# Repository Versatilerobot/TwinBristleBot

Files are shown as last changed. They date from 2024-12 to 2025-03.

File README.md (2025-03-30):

# TwinBristleBot
Vibration-driven locomotion robot <br />
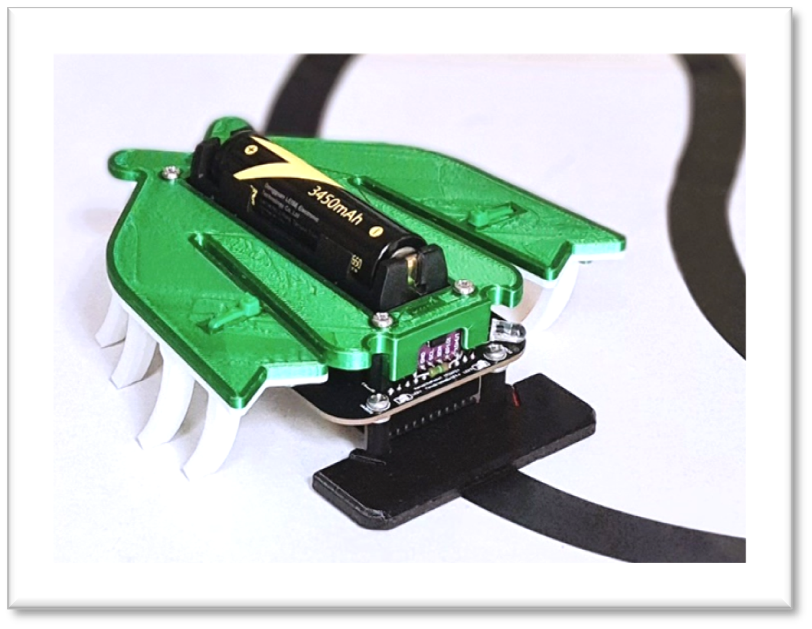
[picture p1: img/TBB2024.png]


# Présentation
La TBB#3 est la troisiéme génération d'un robot propulsé et dirigé par vibrations. Dans ce dossier vous trouverez toutes les informations pour le construire et le programmer en mode suiveur de ligne, mais on peut aussi le téléopérer par Bluetooth. 

Vous trouverez une vidéo de démonstration au lien suivant :
https://youtu.be/ebChETA49Jo

# Historique
Le premier modèle de 2010 avait été conçu à l’aide d’une brosse à balais et un Arduino UNO. Il a fait l’objet d’un tutorial d’assemblage dans la revue Française Planète Robots N°11 à 13. Avec son aspect « SteamPunk » elle a parcouru de longues distances sur les salons.

La deuxième génération de 2016 avait pour objectif d’en faire un kit éducatif pour l’association Française de robotique Caliban https://www.facebook.com/AssoCaliban et pouvait être commandée en Bluetooth par un smartphone. Plus légère et plus rapide elle utilisait des filaments de coupe bordure pour se propulser. Mais son assemblage était assez laborieux et il y avait besoin de plusieurs grosses batteries.
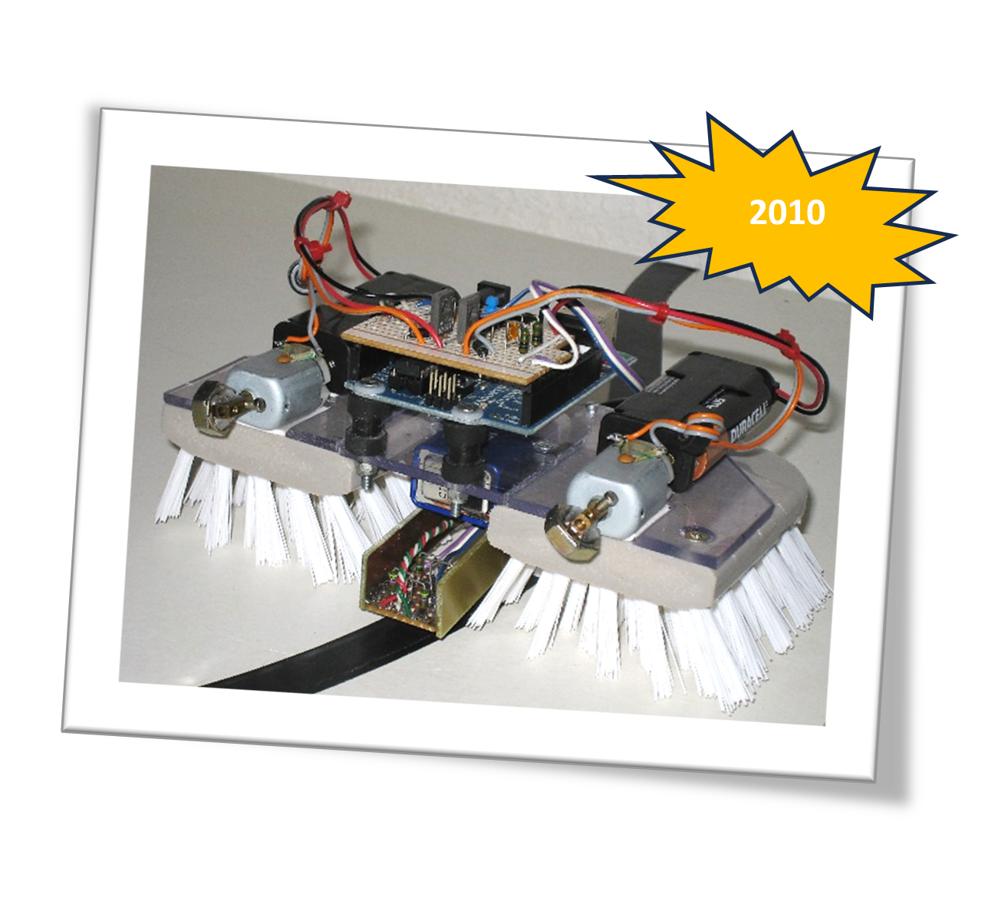
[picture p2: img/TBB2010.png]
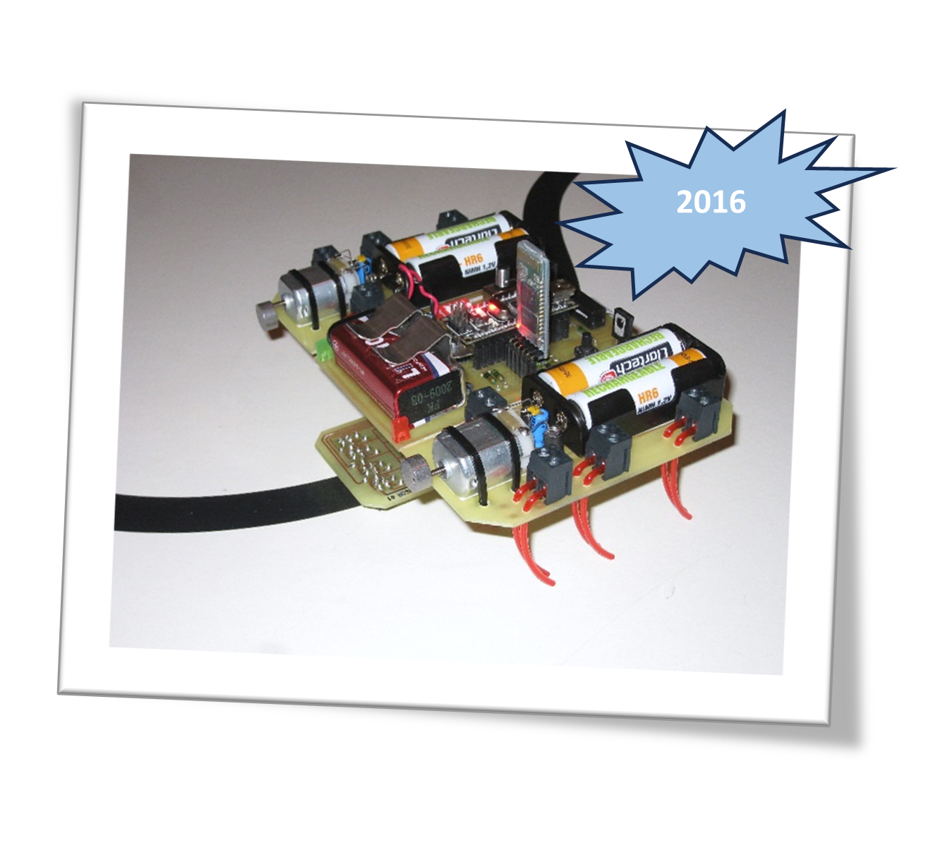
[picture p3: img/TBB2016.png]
 
<br /> Vous retrouverez quelques démos de ces précédentes versions aux lien suivants :<br />
Twin BristleBot 2010 : https://youtu.be/IOm3nyDv1LA?si=ABxqIedQcTU6AHdo <br />
Twin BristleBot 2016: https://youtu.be/aQ-3ZJKfJKs?si=AR1gLndqPDY5ka6K

# Nouvelle version TBB#3
La version de 2024 est conçue en impression 3D PLA pour le corps et en TPU pour les pattes. 
<br /> Tous les plans STL sont fournis.

Le robot est en plus équipé d’un module de télémétrie IR qui utilise la technologie Time Of Flight afin de détecter les obstacles devant lui tel qu'un autre robot ou une barriére. Les vibrations sont générées par deux micro-moteurs à masselottes M20 placés à droite et gauche sous le corps, ce qui permet de diriger le robot. Il a aussi en option la capacité d'émettre et recevoir un code d’indentification IR dont la portée est ajustable électroniquement pour s'identifier et faire évoluer plusieurs robots sur une piste avec croisements. Son module de commande utilise un objet IoT open-source T-Energy équipé d’un ESP32 WROVER-B 240MHZ et qui est alimenté par une batterie 3.7V Li-ion 18650. Le module comporte un connecteur micro USB pour la recharge et la programmation, ainsi qu’un interrupteur d’alimentation.

Pour faire le lien entre le module de commande et les autres composants tel que les moteurs et capteurs j’ai dessiné un PCB double face que j’ai fait réaliser en ligne par JLCPCB https://jlcpcb.com/, mais vous pouvez utiliser tout autre fournisseur.

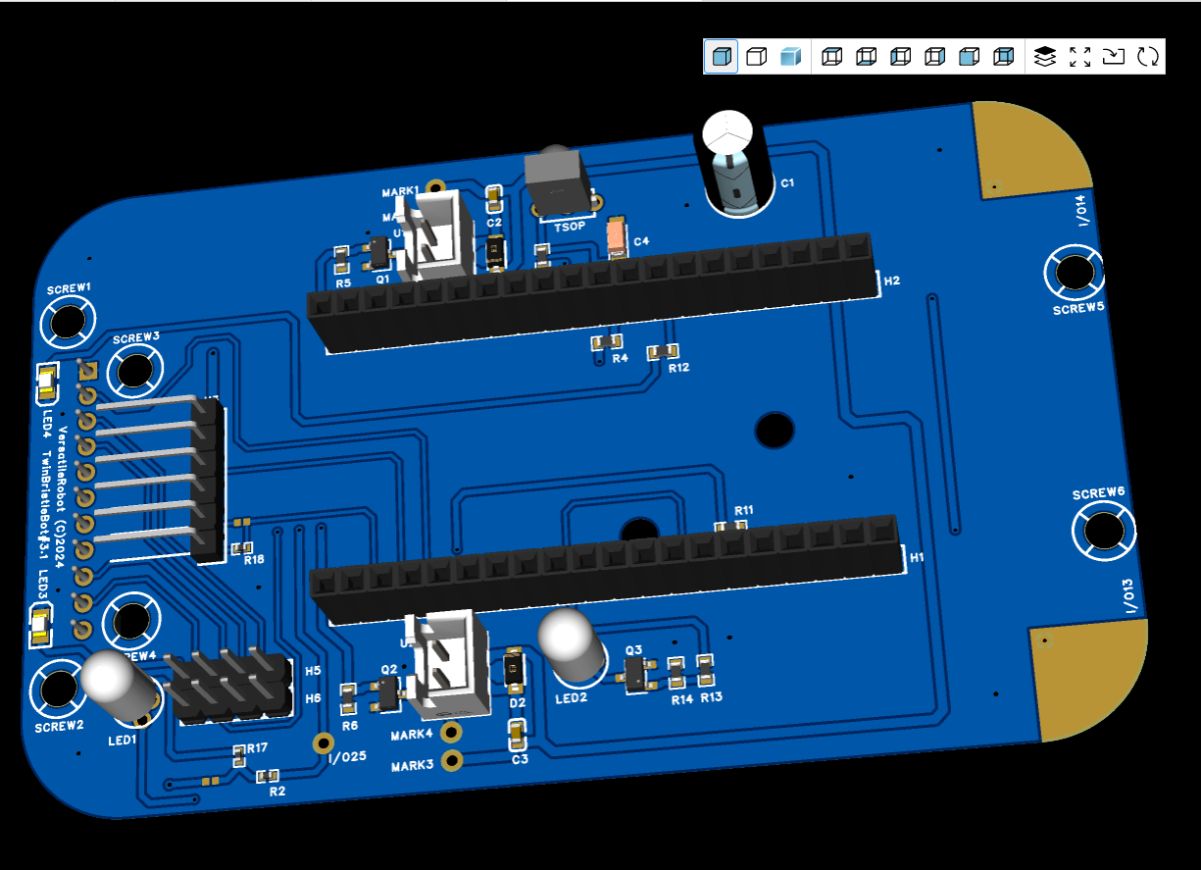
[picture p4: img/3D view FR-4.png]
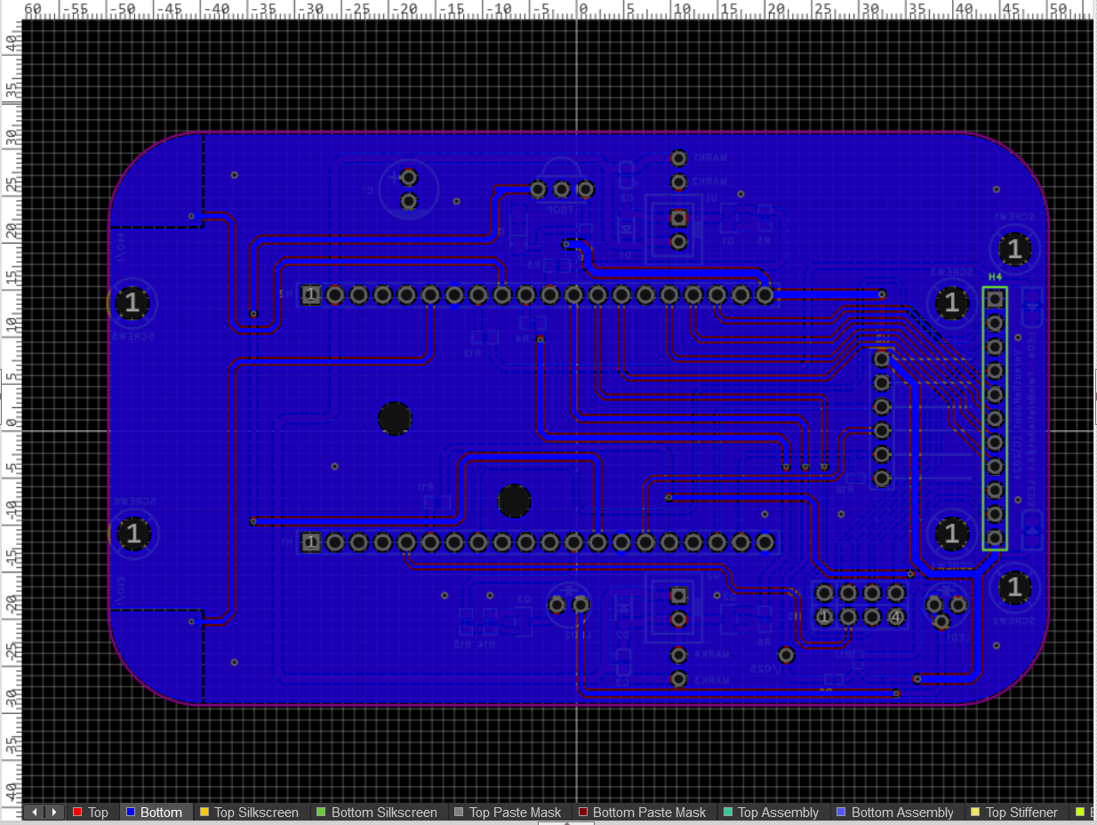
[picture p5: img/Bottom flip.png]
 

Le schéma électronique, ainsi que le fichier Gerber, la BOM de composants et le fichier de placement des composants sont fournis. Pour ma part j’ai opté pour faire assembler les composants de surface SMD (Surface Mount Device), ce qui facilite l’assemblage car il reste à souder soi-même que les composants traditionnels traversants tels que les connecteurs… L’ensemble peut donc être approvisionné en ligne.

Le dossier comprend un manuel d’instructions pour l’assemblage et le démarrage, ainsi qu’un exemple de programme pour suivre une ligne et détecter des obstacles. ( ! ce programme est compatible avec le module complémentaire Expressif version 2.0.17). 
<br /> J'espère que vous apprécierez construire ce robot et si c’est le cas n’hésitez pas à mettre une étoile sur le GitHub, ça fait toujours plaisir.

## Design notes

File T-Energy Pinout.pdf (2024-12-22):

Récapitulatif des I/O possibles pour les pins de l’ESP32 (https://www.upesy.fr/blogs/tutorials/esp32-pinout-reference-gpio-pins-ultimate-guide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)
PIN | TTB#3 | Input | Output | Pullup/Pulldown/Touch pin | Commentaires

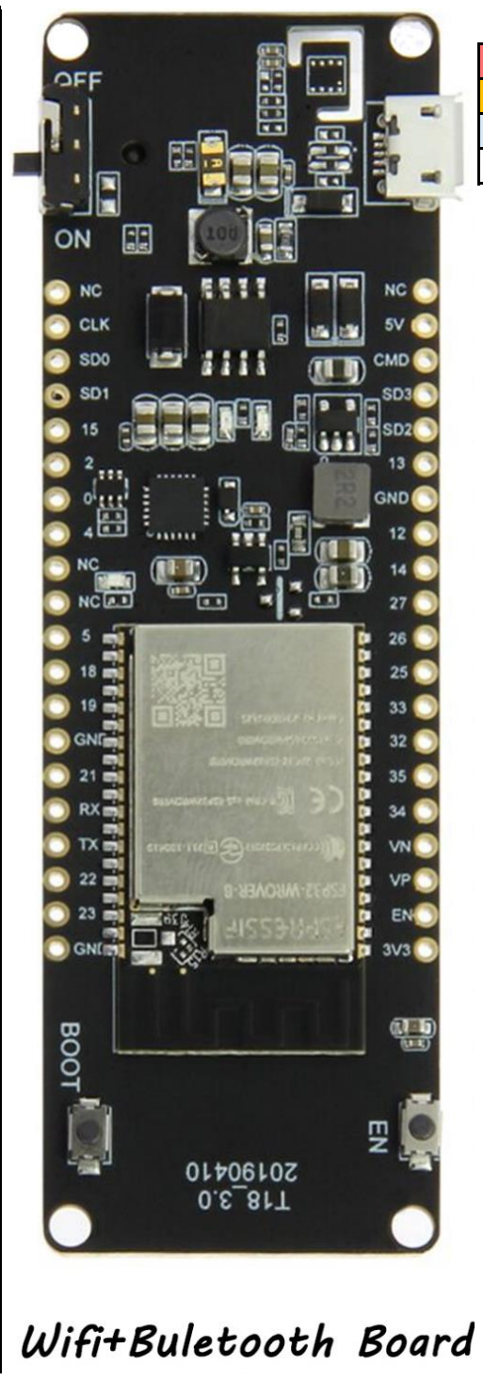
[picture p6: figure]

NC | Recommandé de ne pas utiliser
CLK | NON | NON | Connecté à la flash interne | Peut être utilisé, mais avec certaines précautions
SD0 | NON | NON | Connecté à la flash interne | Fonctionalités réduites
SD1 | NON | NON | Connecté à la flash interne | RAS
15 | Out2 line | OUI | OUI | Pullup interne / TOUCH3 | ADC2_CH3. Startup log si à 3.3V
2 | Red LED | OUI | OUI | Pulldown interne / TOUCH2 | ADC2_CH2. Doit être à 0V pendant le FLASH
0 | Bouton BOOT | OUI | OUI | Pullup interne / TOUCH1 | ADC2_CH1. Doit être à 0V pendant le FLASH
4 | IR line | OUI | OUI | TOUCH0 | ADC2_CH0
NC
NC
5 | Blue Int LED | OUI | OUI
18 | LEDs IR cde | OUI | OUI
19 | Recep IR D | OUI | OUI
GND | GND
21 | I2c ToF | OUI | OUI | | I2C - SDA
RX0 | | OUI | NON | | Communication UART avec le PC
TX0 | | NON | OUI | | Communication UART avec le PC
22 | I2c ToF | OUI | OUI | | I2C - SCL
23 | Enable ToF | OUI | OUI
GND | GND
3.3V | 3.3V
EN | Bouton EN | NON | NON | | Relié au bouton EN (ESP32 Reset)
VP (36) | Out3 line | OUI | NON | Pas de pullup/pulldown interne | ADC1_CH0 à n'utiliser qu'en entrée
VN (39) | Out4 line | OUI | NON | Pas de pullup/pulldown interne | ADC1_CH3 à n'utiliser qu'en entrée
34 | Out5 line | OUI | NON | Pas de pullup/pulldown interne | ADC1_CH6 à n'utiliser qu'en entrée
35 | Bat Voltage | OUI | NON | Pas de pullup/pulldown interne | ADC1_CH7 à n'utiliser qu'en entrée
32 | Out6 line | OUI | OUI | TOUCH9 | ADC1_CH4
33 | Out7 line | OUI | OUI | TOUCH8 | ADC1_CH5
25 | DAC LEDs IR | OUI | OUI | | ADC2_CH8 ; DAC1
26 | Motor1 | OUI | OUI | | ADC2_CH9 ; DAC2
27 | Motor2 | OUI | OUI | TOUCH7 | ADC2_CH7
14 | Digit Sart/Stop | OUI | OUI | TOUCH6
12 | Green LED | OUI | OUI | Pulldown interne / TOUCH5 | Doit être à 0V pendant le BOOT
GND | GND
13 | Digit Speed | OUI | OUI | TOUCH4 | ADC2_CH4
SD2 | | NON | NON | | Connecté à la flash interne
SD3 | | NON | NON | | Connecté à la flash interne
CMD | | NON | NON | | Connecté à la flash interne

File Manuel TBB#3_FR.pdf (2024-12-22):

versatilerobot | TBB#3 | GF 07/12/2024

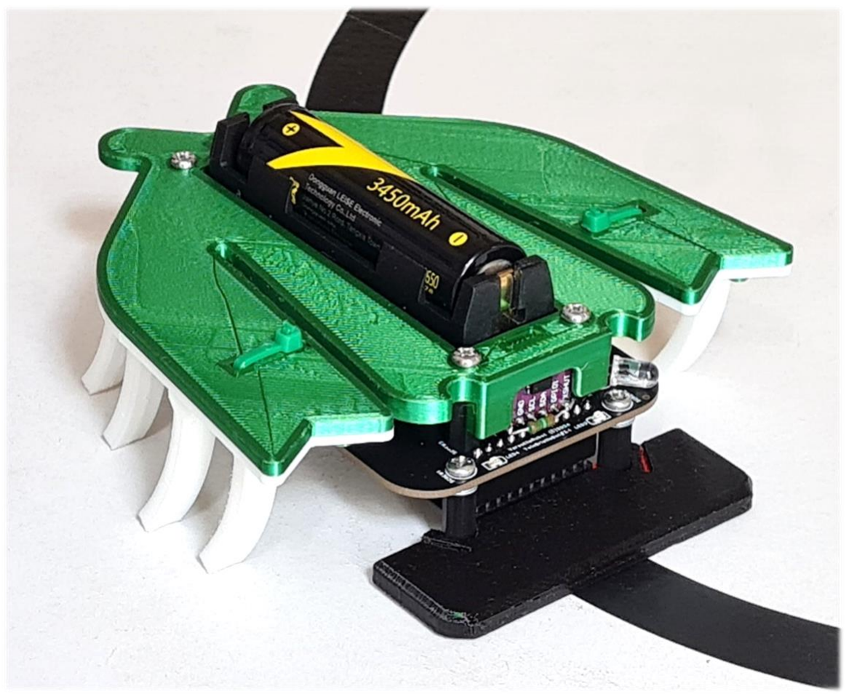
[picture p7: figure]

1 | Version 01

# Manuel TwinBristleBot

## Présentation

La TBB#3 est un robot propulsé et dirigé par vibrations. Il peut selon la programmation suivre une ligne ou être téléopéré par Bluetooth. Vous trouverez dans ce document les instructions pour l’assemblage et le démarrage en mode suiveur de ligne.

Cette vidéo le montre en fonctionnement : https://youtu.be/ebChETA49Jo

Le robot dispose d’un capteur de suivi de ligne infrarouge à 8 canaux. Nous n’en utiliserons que 6 au maximum, mais il y a possibilité de raccorder les deux autres en extrémité si besoin. Il est aussi équipé d’un module VL53L0X de télémétrie IR qui utilise la technologie Time Of Flight afin de détecter les obstacles devant lui et ainsi faire évoluer plusieurs robots à la file sur une même piste.

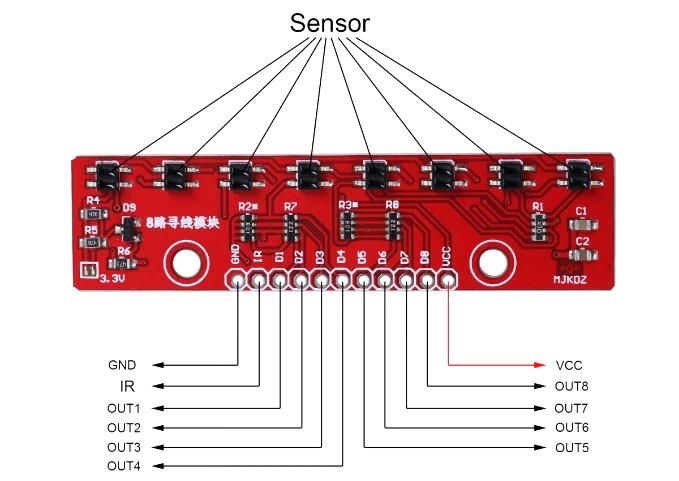
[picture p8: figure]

Les vibrations sont générées par deux micro-moteurs M20 à masselottes placés à droite et à gauche sous le corps, ce qui permet aussi de diriger le robot.

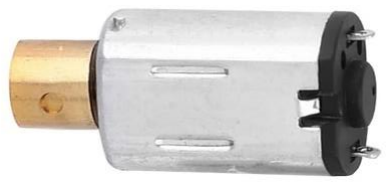
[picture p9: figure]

Rq : Il peut être équipé d’une option émission/réception d’un code d’indentification qui permet à plusieurs robots de se détecter et par exemple céder la priorité à droite. Cette fonction n’est utile que si vous assemblez plusieurs robots dans le but de les faire évoluer ensembles sur une grande piste. Elle est détaillée en page 23 et nécessite d’ajouter quatre composants supplémentaires. Le code étant plus compliqué, je vous invite à ne la tester qu’après avoir assemblé un premier exemplaire dans la version de base décrite ci-après.

Le module de commande utilise un objet IoT open-source T-Energy avec un ESP32 WROVER-B et qui est alimenté par une batterie 3.7V Li-ion 18650 de 3500mAh.

Ce module comporte un connecteur micro USB connecté à un circuit USB-TTL CP2104 et raccordé à un régulateur step-down DC/DC SY8089A1 pour la recharge.

Il est équipé d’un interrupteur d’alimentation et de trois LEDs internes, dont une bleue sur la sortie GPIO 5. La LED rouge indique que le module est en phase de charge batterie et la verte que le chargeur est en stand-by. En outre la pin GPIO 35 est connectée à un pont diviseur pour monitorer l’état de charge de la batterie.

Le module est fourni avec deux barrettes mâles à souder au préalable.

Les pièces du corps et des pattes sont conçues pour être imprimées en 3D et sans supports. Le corps est fait en PLA et les pattes en TPU. Tous les plans STL sont fournis.

Pour faire le lien entre le module de commande et les autres composants tel que les moteurs et capteurs j’ai dessiné un PCB double face que j’ai fait réaliser en ligne par JLCPCB https://jlcpcb.com/, mais vous pouvez utiliser tout autre fournisseur.

Tous les fichiers sont fournis : le schéma électronique, le fichier Gerber, la BOM de composants et le fichier de placement des composants. Pour ma part j’ai opté pour faire assembler les composants de surface SMD (Surface Mount Device), ce qui facilite l’assemblage car il reste à souder par soi-même quelques composants traditionnels traversants tels que les connecteurs… L’ensemble peut donc être approvisionné en ligne.

Le dossier comprend un exemple de sketch pour suivre une ligne et détecter des obstacles.

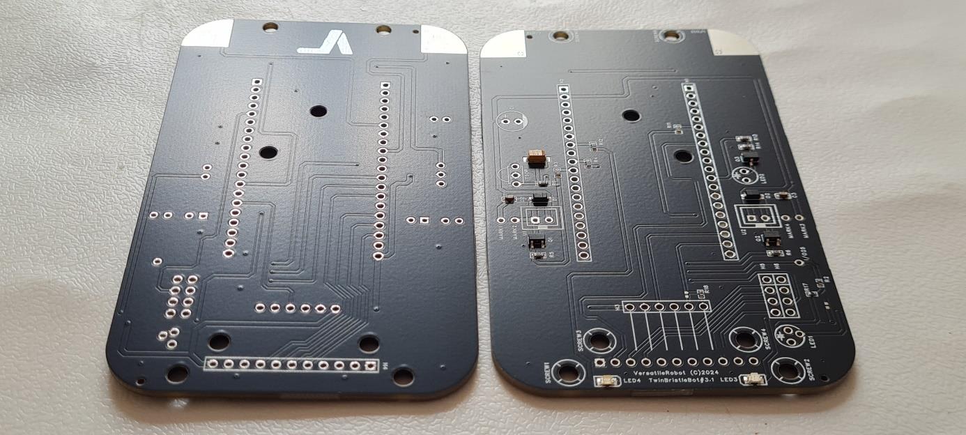
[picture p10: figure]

## Vue d’ensemble de la TBB

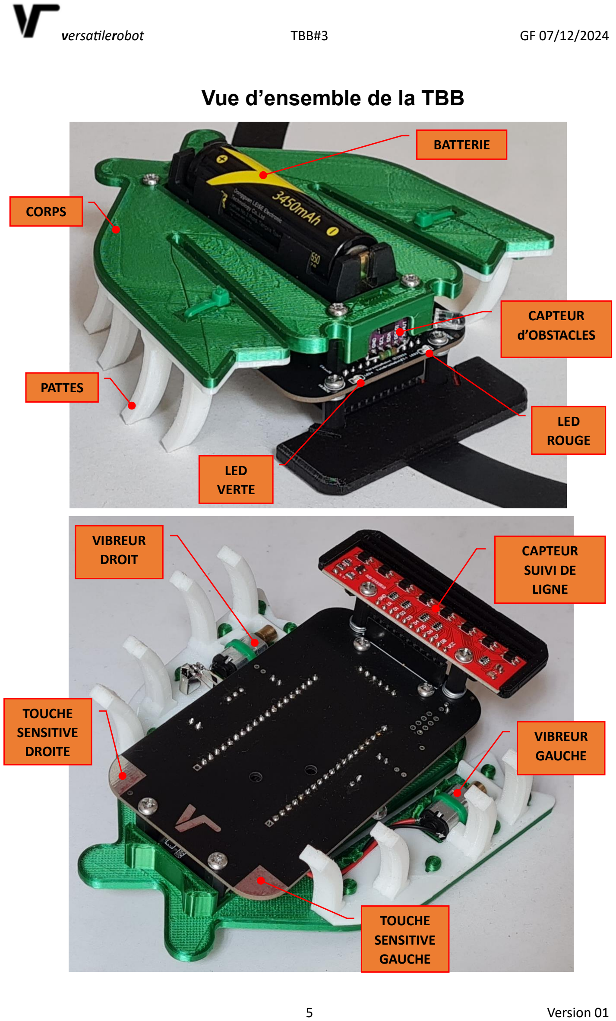
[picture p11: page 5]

CAPTEUR
SUIVI DE
LIGNE

VIBREUR
GAUCHE

VIBREUR
DROIT

TOUCHE
SENSITIVE
DROITE

TOUCHE
SENSITIVE
GAUCHE

CORPS

PATTES

BATTERIE

CAPTEUR
d’OBSTACLES

LED
ROUGE

LED
VERTE

## Nomenclature

Le matériel et les quantités sont détaillées dans le fichier pdf : « BOM TBB#3.pdf (https://github.com/Versatilerobot/TwinBristleBot/blob/6f0d20203dc5283bf4d15a6ebd6a4011ea2f9805/BOM%20TBB%233.pdf) »

Vous y trouverez des liens internet pour l’approvisionnement des pièces avec une estimation de prix. Veuillez noter que je n'ai aucun conflit d'intérêt en lien avec ces sociétés, et que je ne peux pas garantir la disponibilité et/ou le changement de spécifications ou de tarifs.

- Les fichiers pour la réalisation du PCB sont dans le répertoire « PCB (https://github.com/Versatilerobot/TwinBristleBot/tree/046594782c081d072b294108ec4c52680c13fac1/PCB) »

Ce répertoire comprend plusieurs fichiers qui pourront vous être demandés :

- Le dossier gerber compressé pour la réalisation du PCB
- Une BOM composants à souder sur le PCB (SMD et traversants)
- Un fichier de PickAndPlace qui ne comprend que les composants de surface SMD à assembler.
- Le schématique électronique des connections au module T-Energy
- Un fichier représentant les pistes et le placement de composants sur le PCB
- Les fichiers pour l’impression des pièces sont dans le dossier « 3D_STL (https://github.com/Versatilerobot/TwinBristleBot/tree/b6ce86d2bbd25dd28976660b6a2dc0ff41e770cf/3D_STL) »

Ce répertoire comprend quatre plans de pièces à imprimer sans supports et un fichier supplémentaire en option:

- Le Corps de la TBB qui sera à imprimer en PLA, avec une épaisseur de couche de 0,2mm et un remplissage d’au moins 30%. La couleur est libre de choix.
- Un capot de protection pour le capteur de suivi de ligne. Ce capot sert à piéger les reflets parasites externes et augmente ainsi la qualité de détection de la ligne. Il est à imprimer en PLA noir, avec une épaisseur de couche de 0,2mm et un remplissage d’au moins 30%. La couleur noire est préférable pour mieux absorber le rayonnement parasite externe.
- Les Pattes Droite et Gauche qui seront à imprimer en TPU (matériau souple), avec une épaisseur de couche de 0,2mm et un remplissage d’au moins 25%. A noter que les pattes sont dessinées avec une paroi fine qu’il faudra enlever au scalpel après impression. L’avantage de la paroi est d’éviter des rétractations qui sont délicates et génératrices de défauts avec les matériaux souples, comme le « stringing ».
- En option, une barrière pour arrêter la TTB à imprimer en PLA dans un matériau clair ou réfléchissant. Eviter de l’imprimer en noir afin d’avoir la meilleure détection.

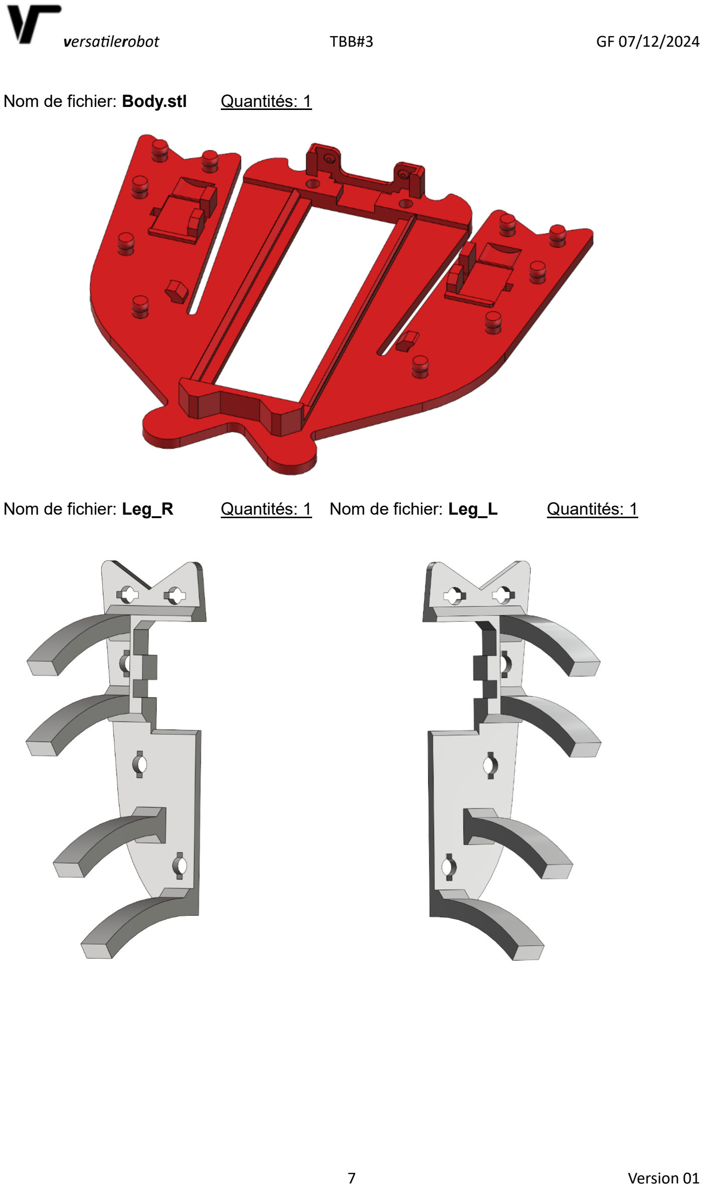
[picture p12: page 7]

Nom de fichier: Body.stl | Quantités: 1
Nom de fichier: Leg_R | Quantités: 1 Nom de fichier: Leg_L | Quantités: 1

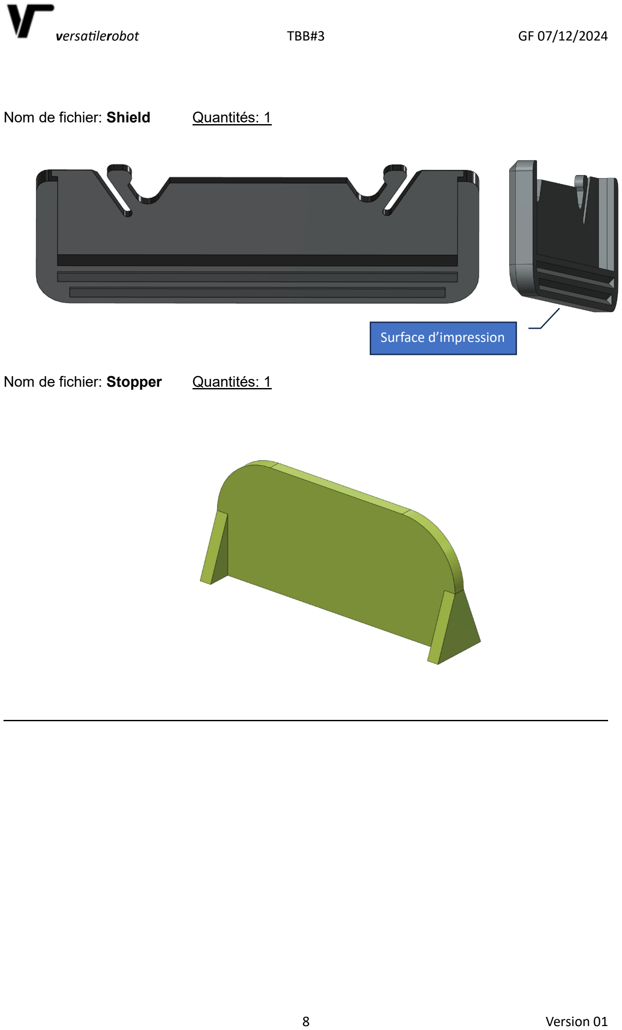
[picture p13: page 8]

Nom de fichier: Shield | Quantités: 1
Nom de fichier: Stopper | Quantités: 1

Surface d’impression

## Assemblage du Robot

Utilisez les images pour vous aider à positionner les composants. Utilisez la sérigraphie du PCB pour vérifier le sens de montage.

Soudez les composants traversants:

1 x PCB avec composants SMD déjà soudés
3 x Barrettes femelle 20 pins 2,54mm
2 x Prises femelles à souder (fournies avec les câbles moteurs)
1 x Connecteur mâle angle droit 6 Pins
- Souder les 2 prises femelle qui serviront à raccorder les moteurs
! attention au sens de montage.
- Souder le connecteur mâle à angle droit 6 Pins du télémètre IR
- Souder les 2 barrettes 20 Pins qui serviront à raccorder le module T-Energy Vous pouvez les enficher sur le module T-Energy temporairement pour faciliter le placement des barrettes à la verticale.

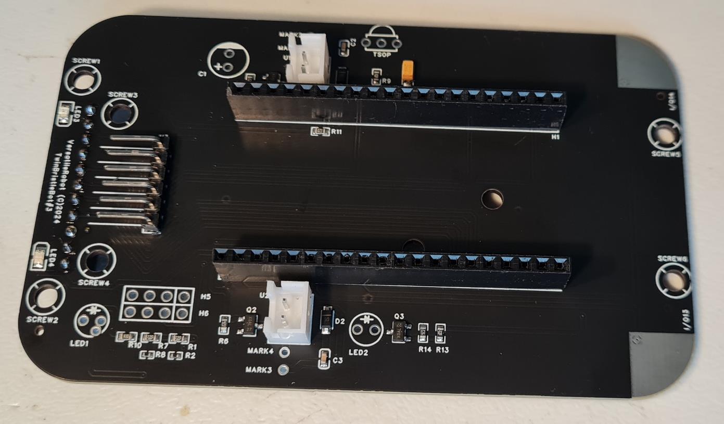
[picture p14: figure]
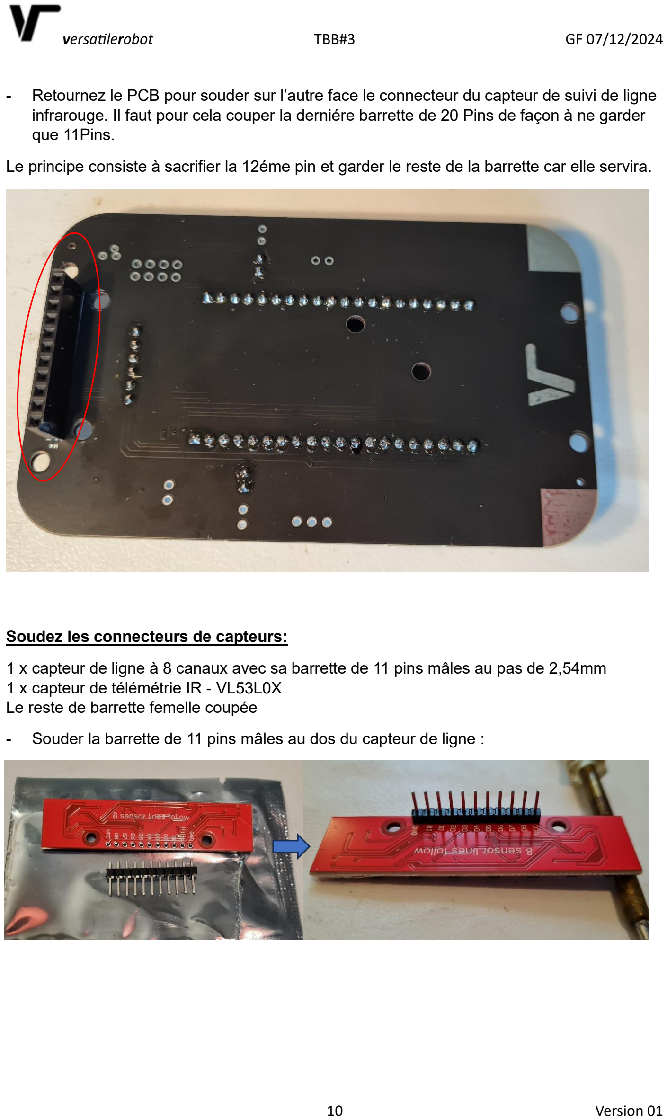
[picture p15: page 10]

- Retournez le PCB pour souder sur l’autre face le connecteur du capteur de suivi de ligne infrarouge. Il faut pour cela couper la derniére barrette de 20 Pins de façon à ne garder que 11Pins.

Le principe consiste à sacrifier la 12éme pin et garder le reste de la barrette car elle servira.

Soudez les connecteurs de capteurs:

1 x capteur de ligne à 8 canaux avec sa barrette de 11 pins mâles au pas de 2,54mm 1 x capteur de télémétrie IR - VL53L0X
Le reste de barrette femelle coupée
- Souder la barrette de 11 pins mâles au dos du capteur de ligne :

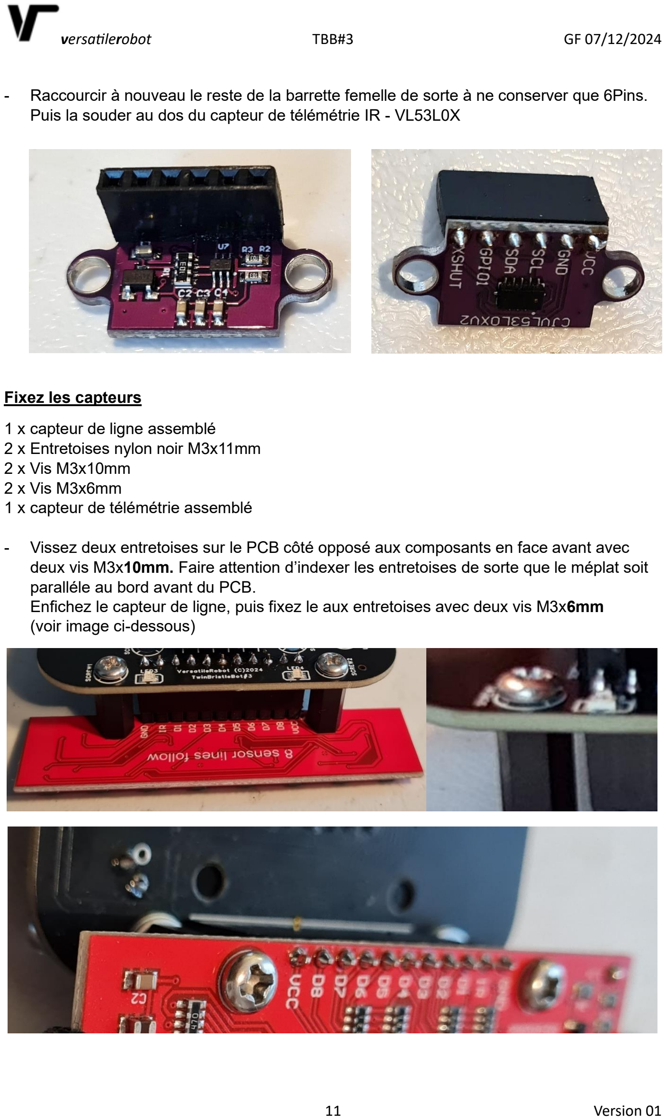
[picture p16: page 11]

- Raccourcir à nouveau le reste de la barrette femelle de sorte à ne conserver que 6Pins. Puis la souder au dos du capteur de télémétrie IR - VL53L0X

Fixez les capteurs

1 x capteur de ligne assemblé
2 x Entretoises nylon noir M3x11mm 2 x Vis M3x10mm
2 x Vis M3x6mm
1 x capteur de télémétrie assemblé
- Vissez deux entretoises sur le PCB côté opposé aux composants en face avant avec deux vis M3x10mm. Faire attention d’indexer les entretoises de sorte que le méplat soit paralléle au bord avant du PCB.
Enfichez le capteur de ligne, puis fixez le aux entretoises avec deux vis M3x6mm (voir image ci-dessous)

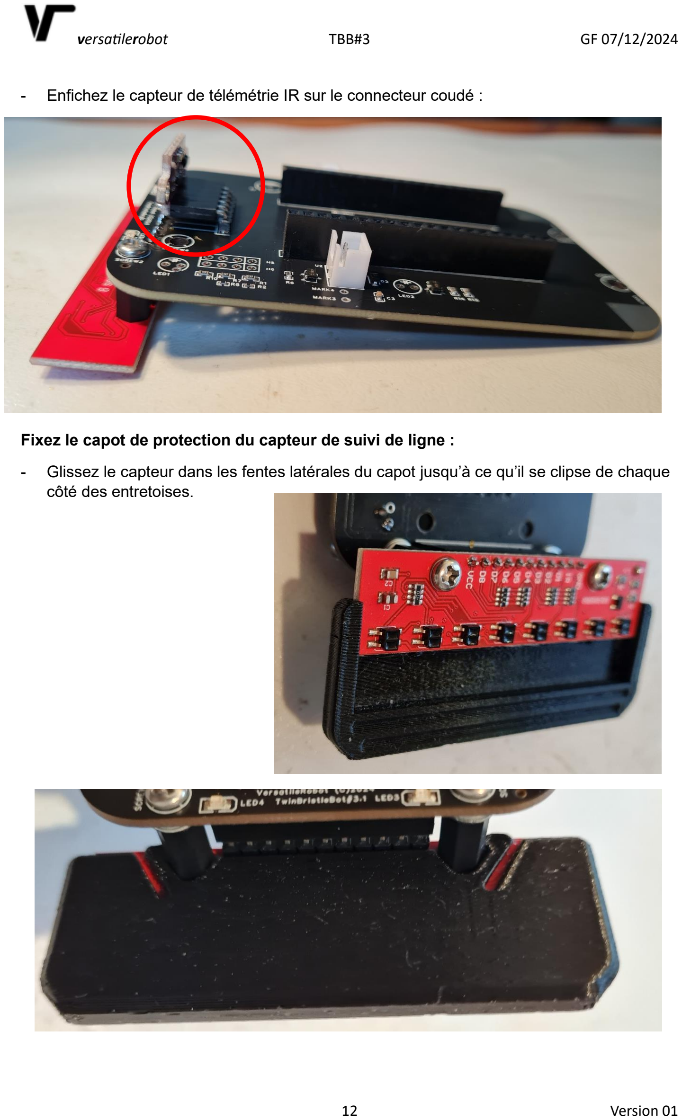
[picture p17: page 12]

- Enfichez le capteur de télémétrie IR sur le connecteur coudé :

Fixez le capot de protection du capteur de suivi de ligne :

- Glissez le capteur dans les fentes latérales du capot jusqu’à ce qu’il se clipse de chaque côté des entretoises.

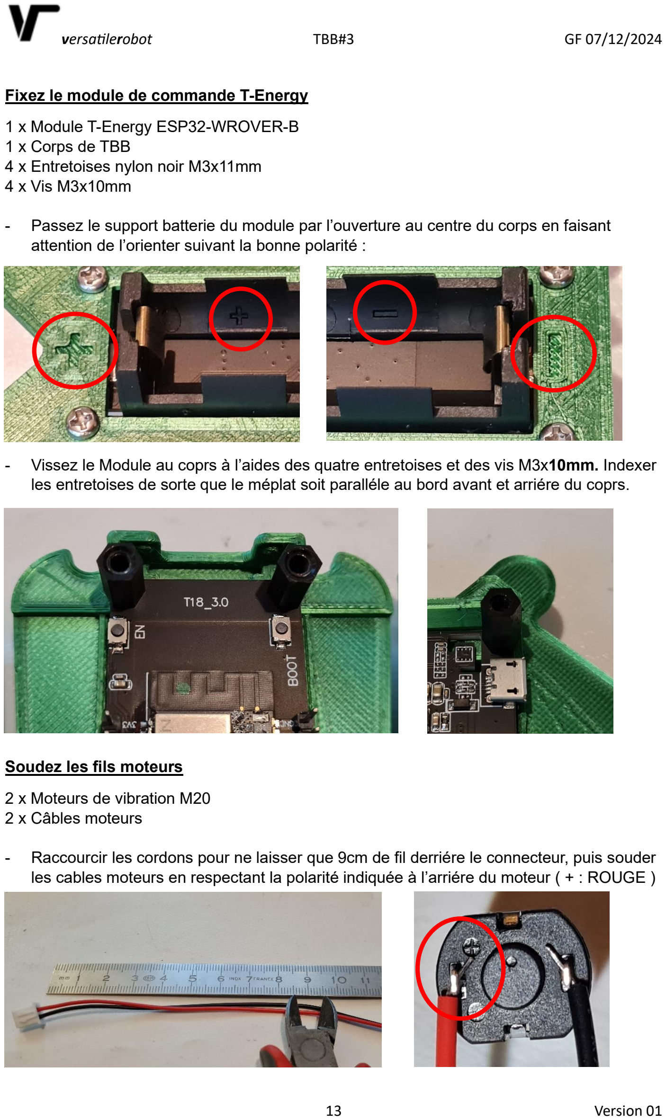
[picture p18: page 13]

Fixez le module de commande T-Energy

1 x Module T-Energy ESP32-WROVER-B 1 x Corps de TBB
4 x Entretoises nylon noir M3x11mm
4 x Vis M3x10mm
- Passez le support batterie du module par l’ouverture au centre du corps en faisant attention de l’orienter suivant la bonne polarité :
- Vissez le Module au coprs à l’aides des quatre entretoises et des vis M3x10mm. Indexer les entretoises de sorte que le méplat soit paralléle au bord avant et arriére du coprs.

Soudez les fils moteurs

2 x Moteurs de vibration M20
2 x Câbles moteurs
- Raccourcir les cordons pour ne laisser que 9cm de fil derriére le connecteur, puis souder les cables moteurs en respectant la polarité indiquée à l’arriére du moteur ( + : ROUGE )

Montez les moteurs et les pattes

2 x Moteurs de vibration M20 avec câble
2 x Pattes imprimées en TPU (1 Droite ; 1 Gauche)
2 x Attaches de câble en nylon autobloquant 3x100mm
- Les moteurs se fixent avec les attaches de câble en nylon autobloquantes.
Faire très attention à ce que la masselotte soit libre et n’entre pas en contact avec les pièces. Une astuce consiste à placer un morceau de ruban collant double face sous le moteur pour le maintenir dans son emplacement le temps de serrer l’attache.
Serrer suffisamment l’attache pour que le moteur ne bouge pas, puis couper l’excédent.

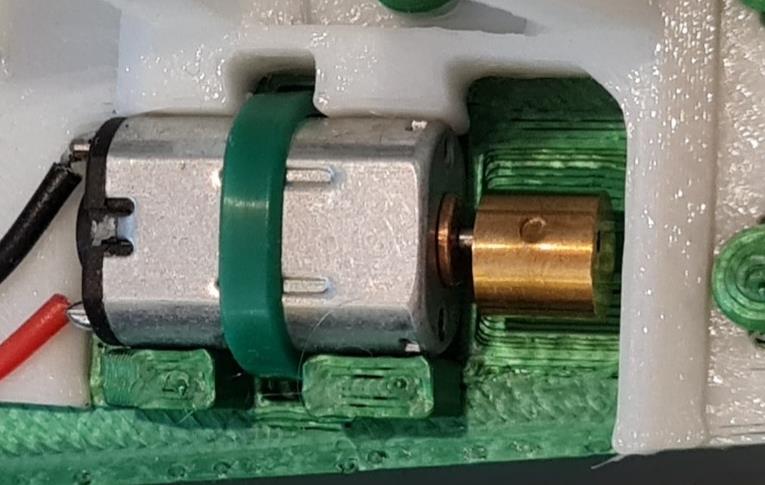
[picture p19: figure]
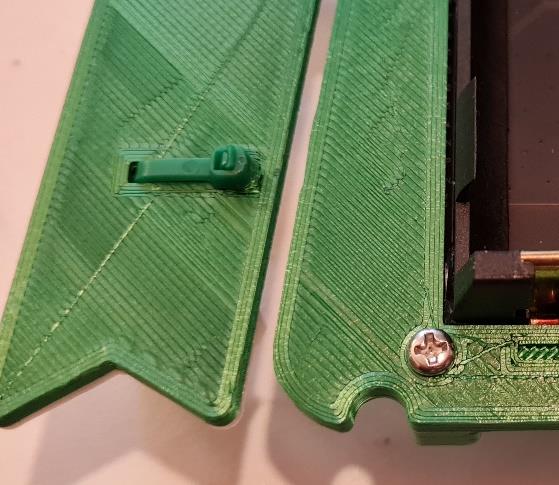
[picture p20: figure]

- Clipser chaque patte sur les 5 plots imprimés du corps de la TBB. Procédez plot par plot en appuyant de chaque côté des trous de sorte que l’ergot passe à travers. Evitez les efforts latéraux qui risqueraient de casser un plot et mettre hors d’usage la pièce.
- La base des pattes doit être en contact plan avec le corps de la TBB une fois clipsée. Ne pas oublier de faire passer le câble moteur dans l’attache prévue pour le maintenir avant de clipser le dernier plot arrière.

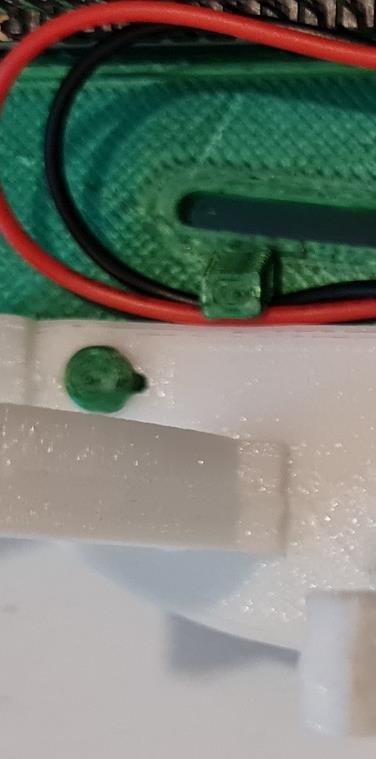
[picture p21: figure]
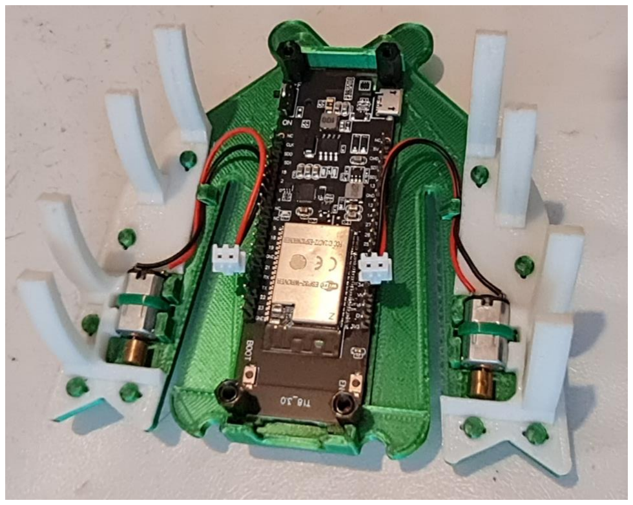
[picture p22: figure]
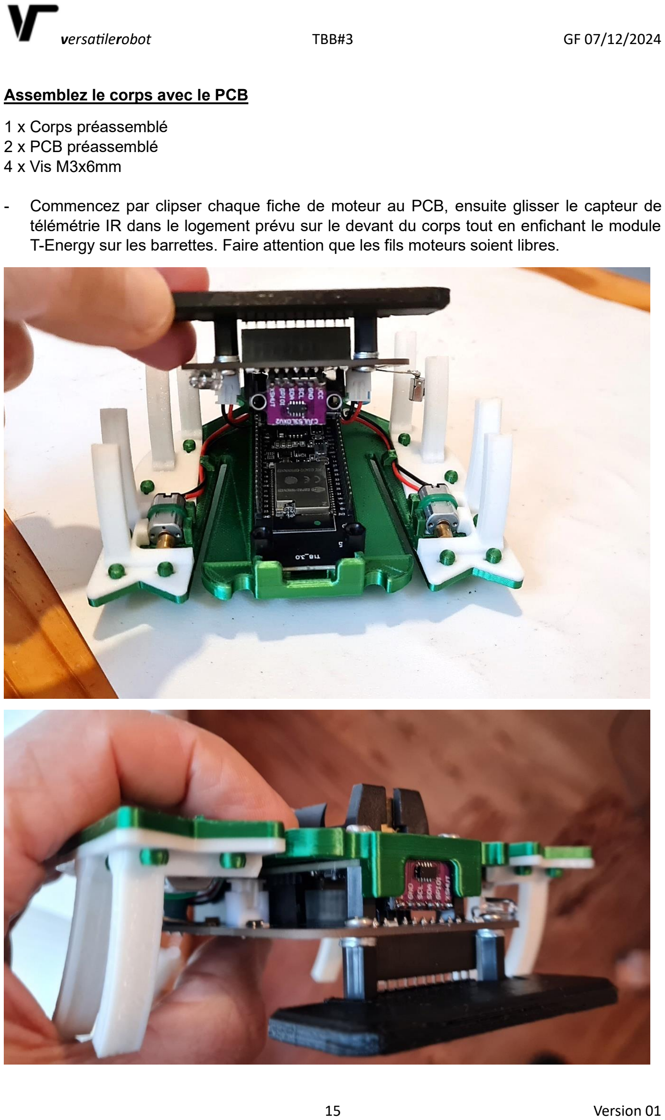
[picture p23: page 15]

Assemblez le corps avec le PCB

1 x Corps préassemblé
2 x PCB préassemblé
4 x Vis M3x6mm
- Commencez par clipser chaque fiche de moteur au PCB, ensuite glisser le capteur de télémétrie IR dans le logement prévu sur le devant du corps tout en enfichant le module T-Energy sur les barrettes. Faire attention que les fils moteurs soient libres.

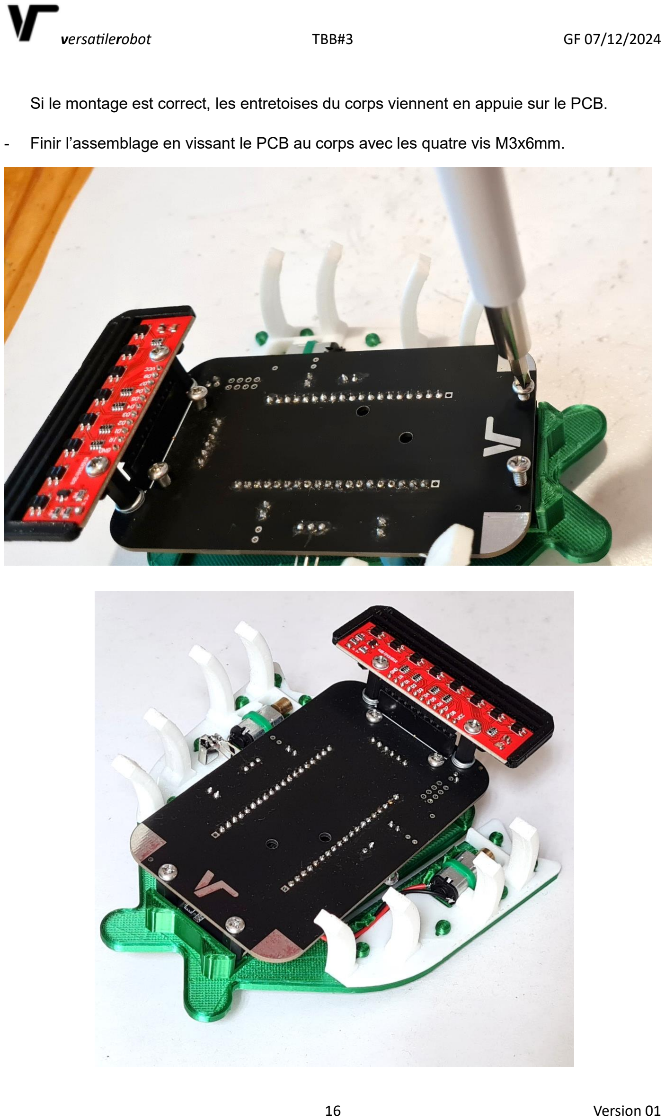
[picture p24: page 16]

Si le montage est correct, les entretoises du corps viennent en appuie sur le PCB.

- Finir l’assemblage en vissant le PCB au corps avec les quatre vis M3x6mm.

Vérifiez la hauteur du capteur de ligne

1 x TTB#3
Rondelles M3

Il est important de contrôler la hauteur du capteur par rapport au sol. La notice du capteur indique une distance maximale de 3mm/sol. Mais l’expérience montre qu’une distance de 2mm maxi est préférable.

- Monter la batterie dans son emplacement pour que la TBB fasse son poids en fonctionnement. ! Attention au bon respect des polarités car le module T-Energy n’est pas protégé contre l’inversion de tension.
- Une fois la pile montée, mesurer la hauteur entre le bouclier / sol, qui est identique à celle des capteurs / sol.
- Enlever la pile puis dévisser les entretoises de capteur par le haut (il y a une encoche dans la forme pour passer un tournevis.
- Ajouter la quantité de rondelles nécessaires entre le PCB et les entretoises du capteur pour ne pas dépasser les 2mm / sol.

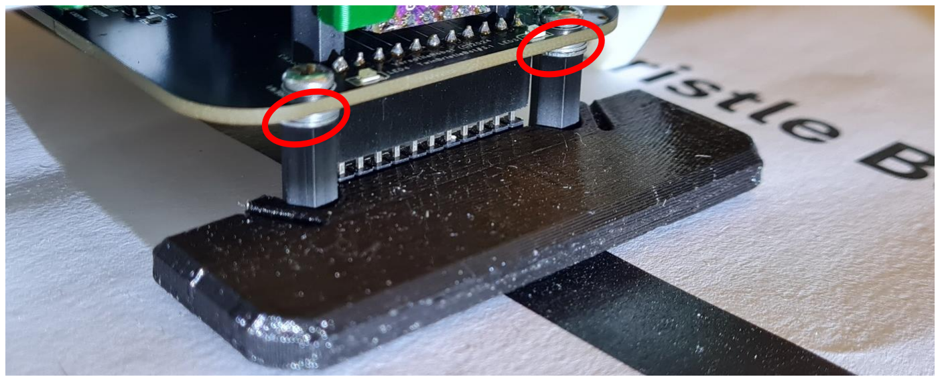
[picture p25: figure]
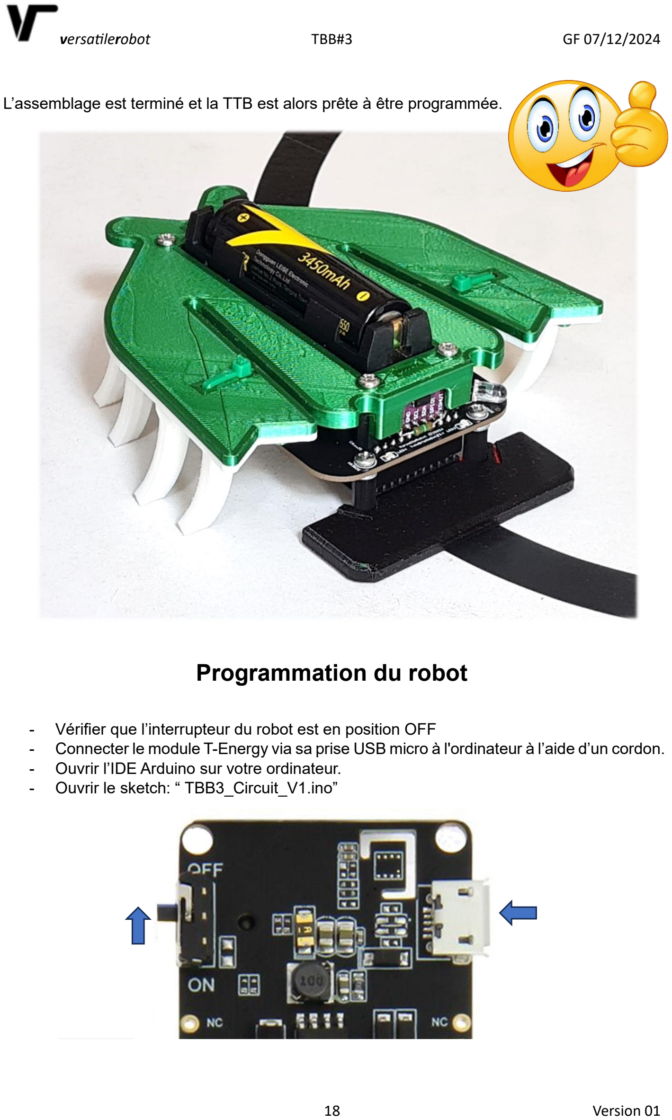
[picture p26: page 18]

L’assemblage est terminé et la TTB est alors prête à être programmée.

## Programmation du robot

- Vérifier que l’interrupteur du robot est en position OFF
- Connecter le module T-Energy via sa prise USB micro à l'ordinateur à l’aide d’un cordon.
- Ouvrir l’IDE Arduino sur votre ordinateur.
- Ouvrir le sketch: “ TBB3_Circuit_V1.ino”

Installation de l’ESP32 wrover dans l’IDE Arduino

- Cliquer sur “Fichier” dans la barre de menus, puis sélectionner “Préférences”.
- Dans la fenêtre des préférences, rechercher le champ “URL de gestionnaire de cartes supplémentaires” et cliquer sur le bouton à droite pour le modifier.
- Ajouter l’URL suivante dans le champ :
- « https://raw.githubusercontent.com/espressif/arduino-esp32/gh-pages/package_esp32_index.json (https://raw.githubusercontent.com/espressif/arduino-esp32/gh-pages/package_esp32_index.json) »
- Cliquer sur le bouton “OK” pour fermer la fenêtre des préférences.

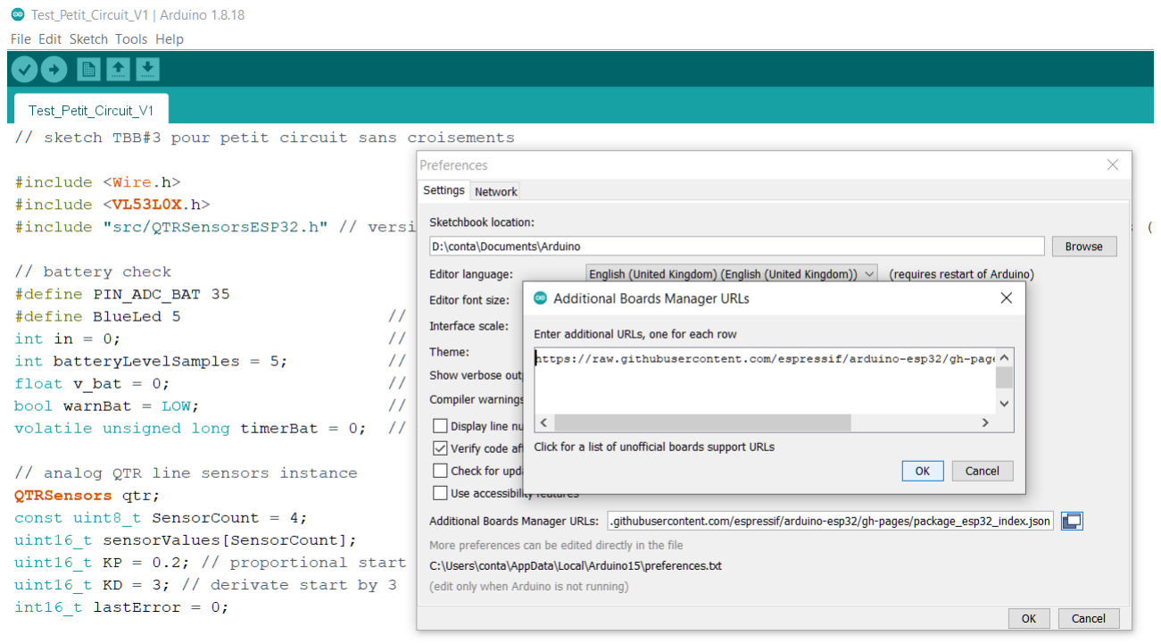
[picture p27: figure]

- Maintenant, aller dans le menu “Outils” > “Type de carte” > “Gestionnaire de cartes”.
- Descendre tout en bas jusqu’à trouver esp32 et cliquer sur installer.
- Une fois que le téléchargement et l’installation sont terminés les cartes ESP32 ont été rajoutées dans le gestionnaire de carte.
- Fermer le gestionnaire de cartes.

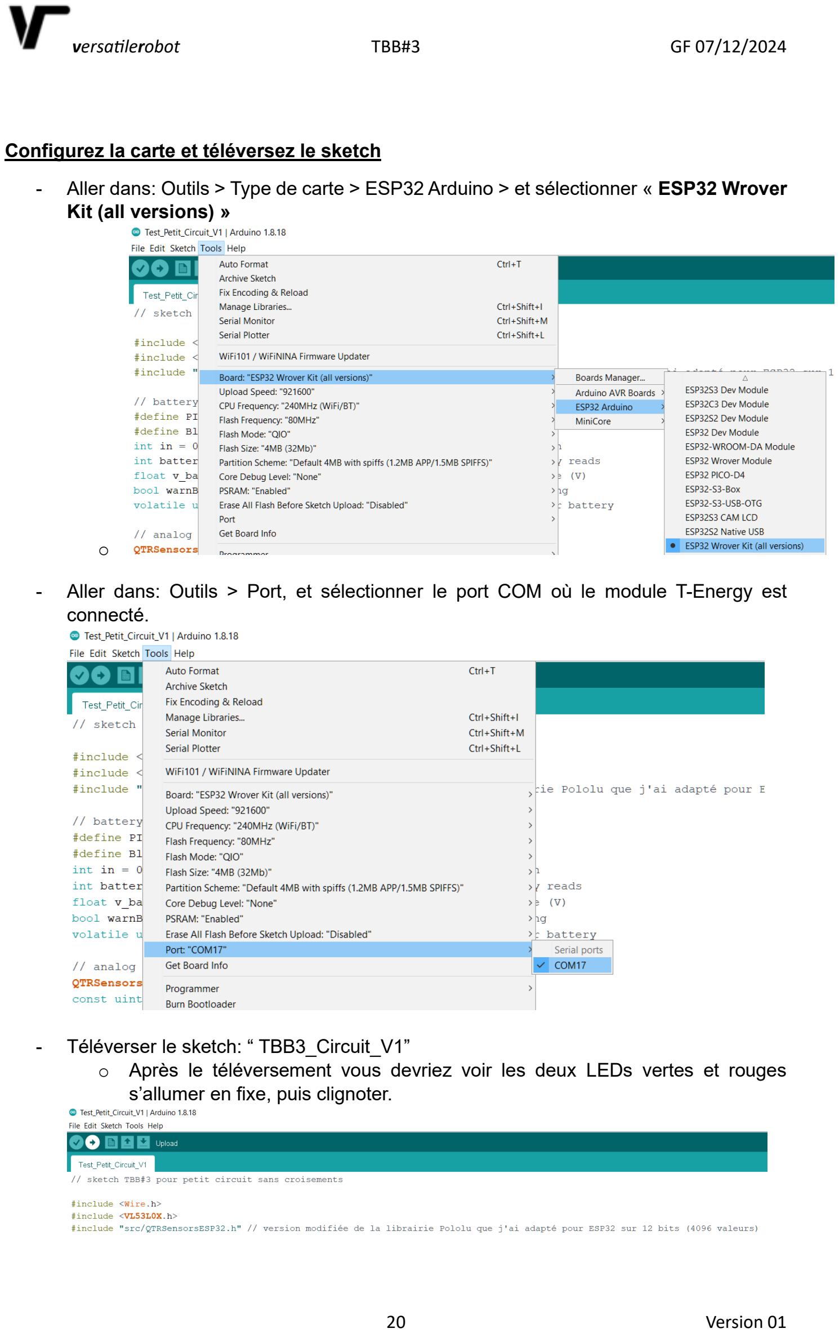
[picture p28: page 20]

Configurez la carte et téléversez le sketch

- Aller dans: Outils > Type de carte > ESP32 Arduino > et sélectionner « ESP32 Wrover Kit (all versions) »

o

- Aller dans: Outils > Port, et sélectionner le port COM où le module T-Energy est connecté.
- Téléverser le sketch: “ TBB3_Circuit_V1”
- Après le téléversement vous devriez voir les deux LEDs vertes et rouges s’allumer en fixe, puis clignoter.

## Fabrication de la piste

Une piste d’essai est proposée dans le fichier pdf : « Petit_Circuit_2xA3 (https://github.com/Versatilerobot/TwinBristleBot/blob/4eece94783c6f0f59b3dd151248d4fdfa35608ea/Petit_Circuit_2xA3.pdf) »

Cette piste est destinée à être imprimée en deux volets, chacun ayant un format A3.

La piste a donc une dimension hors-tout de 42 x 59,4 cm, soit un format A2.

Il est recommandé d’imprimer cette piste avec une imprimante laser sur du papier blanc et une encre noire compatible avec les systèmes de suivi de ligne infrarouge. Attention : Certaines encres noires, comme celles parfois utilisées dans les imprimantes photo peuvent ne pas fonctionner car elles contiennent des composants qui réfléchissent les infrarouges.

En alternative, si vous n’avez pas la possibilité d’imprimer une piste vous pouvez utiliser du ruban adhésif électrique noir de largeur 19mm

! La TBB est un robot de la famille des « VibroBots », ce qui nécessite qu’il évolue sur un sol dur pour renvoyer l’énergie des vibrations. De fait la piste doit être collée sur une surface rigide (plaque de contreplaqué ou cartonnée épaisse) et placée sur une table ou un sol dur. (moquette interdite)

Veuillez aussi considérer que :

Ce mode de locomotion engendre un grip au sol faible. De fait le robot peut drifter et s’écarter de la trajectoire si les virages sont trop resserrés ou si elle va trop vite.

Il faut faire attention à ce qu’il n’y ait pas d’aspérités qui pourraient accrocher les pattes.

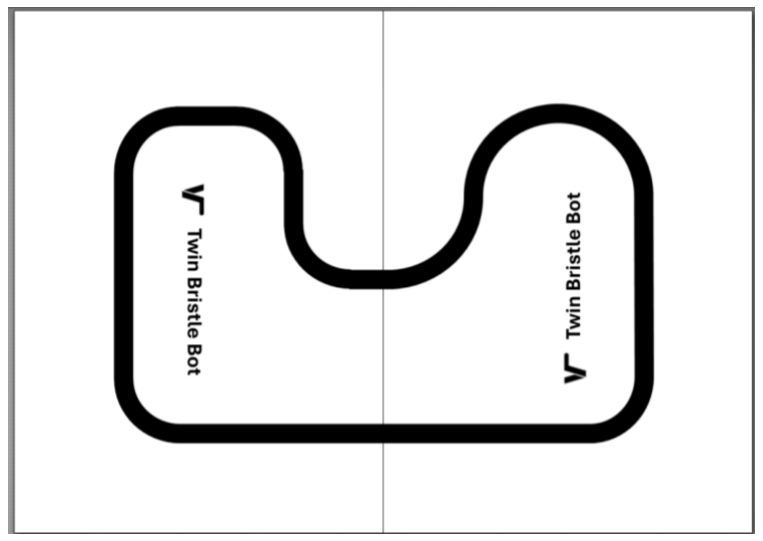
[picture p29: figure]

## Mise en marche

La procédure de mise en marche est très rapide et passe par une phase d’apprentissage du contraste de la ligne. Il faut d’abord monter une batterie chargée dans son emplacement en faisant toujours bien attention de respecter les polarités.

Calibration

- Basculer l’interrupteur de mise en marche sur la position ON
- Placer rapidement la TBB centrée sur la ligne noire de la piste sans la lâcher.
Après un court instant les deux LED verte et rouge s’allument en fixe.
- Faire glisser de droite à gauche la TBB sans la soulever du sol de sorte que le capteur de ligne la balaye sur toute sa largeur.
- Après quelques instants les LEDs se mettent à clignoter.

Démarrage

- Appuyer sur la touche sensitive de Droite pour la faire démarrer.

Arrêt

- Appuyer à nouveau sur la touche de Droite pour l’arrêter.
- Une autre méthode plus facile consiste à stopper la TBB en plaçant une main ou un objet devant elle. Vous pouvez utiliser le « Stopper » dont le plan est fourni. Ensuite, appuyer avec l’autre main sur la touche sensitive de Droite pour valider l’arrêt.
- Lorsque l’arrêt est validé les LED se remettent à clignoter.
- Si vous ne validez pas l’arrêt, alors la TBB repartira dés que l’obstacle sera retiré.

Sélection de la vitesse

- La sélection de vitesse fonctionne qu’après la calibration et lorsque la TBB est à l’arrêt.
- Faites un appuie long sur la touche sensitive de Gauche pour incrémenter la vitesse, puis la relâcher.
- Pour savoir quelle vitesse est sélectionnée il faut compter le nombre de clignotements faits par n’importe laquelle des deux diodes.
- | 1 flash : | Vitesse lente
- | 2 flashs : | Vitesse moyenne (sélectionnée par défaut au démarrage)
- | 3 flashs : | Vitesse maximale
- A chaque séquence d’appuie long on passe d’une vitesse à la suivante.
- Une fois la vitesse sélectionnée, appuyer sur la touche sensitive de droite pour redémarrer la TBB.

Option : Emission/détection d’un code d’identification

Le robot peut être équipé d’une fonction expérimentale pour l’émission/détection d’un code d’identification. Cela permet à plusieurs robots évoluant sur une même piste de s’identifier, et par exemple de céder la priorité à droite lorsqu’ils arrivent simultanément à un croisement.

Pour cela on utilise un détecteur IR TL1838 discriminé à 38kHz. Ce composant nécessite une capacité chimique de filtrage de 10µf. L’émission est assurée par deux diodes infrarouge 5MM 940nm montées en série et dont la portée est ajustable électroniquement à l’aide de l’une des deux sortie DAC de l’ESP32

Les composants sont identifiés dans la BOM générale et ils se montent sur le PCB en suivant la disposition indiquée par la sérigraphie. Il est préférable d’écarter le plus possible le récepteur du PCB afin qu’il ne soit pas masqué par les pattes du robot. Quant aux diodes, les pattes sont elles aussi pliées pour émettre à l’horizontale.


Le codage de l’ID utilise le protocole NEC. Cela permet d’envoyer rapidement l’information en impactant le moins possible le temps de cycle.

Vous trouverez un exemple de sketch: “Send_Receive_ID.ino” pour tester la fonction et à insérer dans votre propre programme pour l’utiliser.

J'espère que vous apprécierez construire ce robot et si c’est le cas n’hésitez pas à mettre une étoile sur le GitHub, (https://github.com/Versatilerobot/TwinBristleBot) ça fait toujours plaisir.

Auteur

Guy Feuilloley, alias VersatileRobot

https://www.facebook.com/versat.ilerobot

Copyright (c) 2024 Versatilerobot

L'Auteur ne donne aucune garantie et n'accepte aucune responsabilité quant à l'exactitude ou à l'exhaustivité des informations et des matériaux contenus dans ce manuel d'instructions. En aucun cas l'Auteur ne sera tenu responsable de quelque manière que ce soit des réclamations, dommages, pertes, dépenses ou responsabilités, y compris, sans limitation, tout dommage direct, indirect ou consécutif résultant ou découlant directement ou indirectement de la fabrication ou de l'utilisation de ce robot, ainsi que de son fonctionnement ou sa durée de vie.

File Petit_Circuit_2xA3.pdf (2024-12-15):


Twin Bristle Bot


Twin Bristle Bot

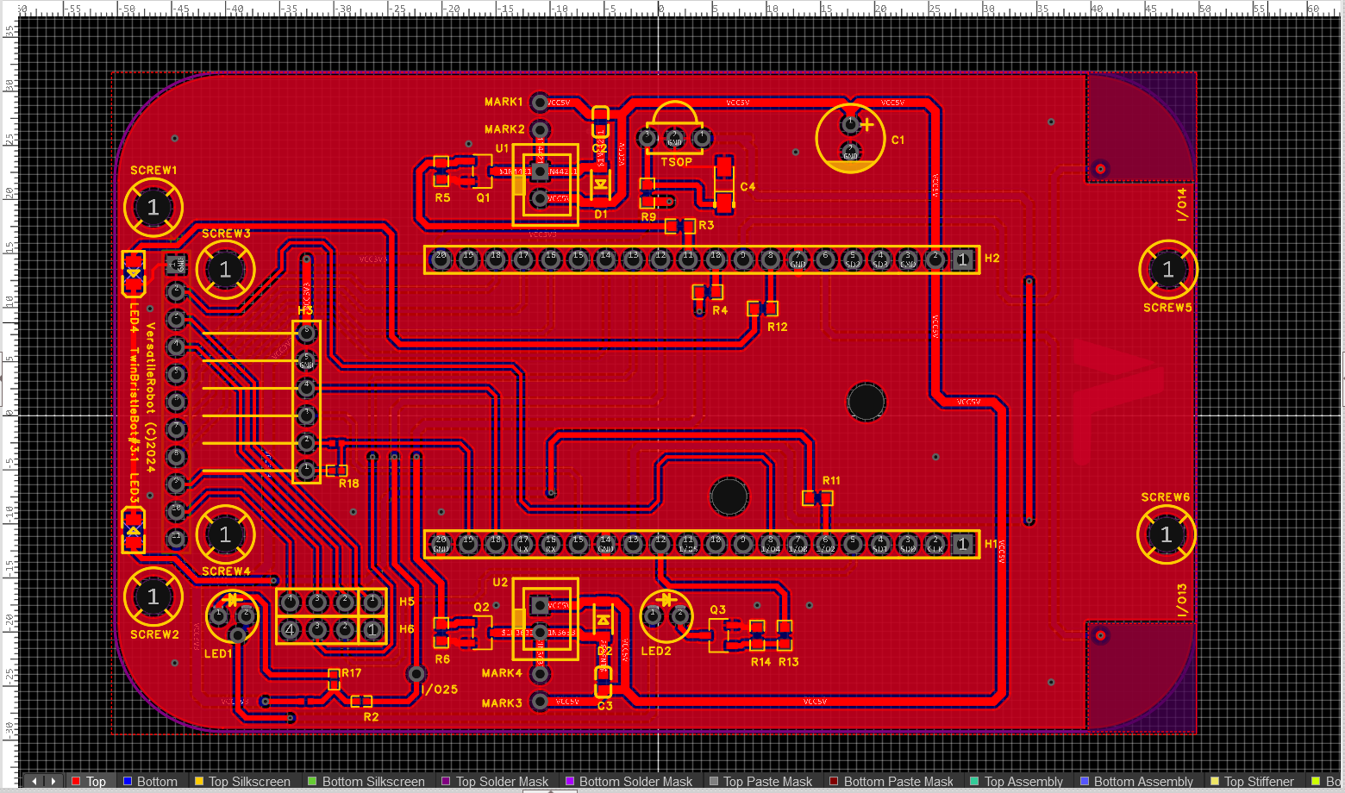
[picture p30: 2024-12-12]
img/Top.png

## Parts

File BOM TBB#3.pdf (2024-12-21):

GF | BOM TBB#3.xlsx | 21/12/2024

Composants
électroniques

Quantité
par robot

Prix
Unitaire €

Prix total
€
| | | | Notes | Exemples de fourniture
Moteurs de vibration | 2 | 4,94 | 9,87 | Mini moteur de vibration M20 | 3Pcs Mini moteur de vibration CC 6V 1000RPM M20 (https://www.amazon.fr/dp/B07WP2PGBW?ref_=ppx_hzod_title_dt_b_fed_asin_title_0_1)
Câbles moteurs | 2 | 0,34 | 0,69 | Câble JST XH avec prise femelle à 2 broches, pas de 2.54mm | Câble JST XH avec prise femelle à 2 broches (https://fr.aliexpress.com/item/1005005902593401.html)
Carte energie ESP32-WROVER-B | 1 | 8,49 | 8,49 | TTGO T-Energy ESP32 8 Mbytes, with separate pin header strip | TTGO T-Energy ESP32 8MByte (https://fr.aliexpress.com/item/1005005489393083.html?src=google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)
Capteur de ligne IR à 8 Canaux | 1 | 2,21 | 2,21 | Capteur de suivi infrarouge à 8 canaux IR | Capteur de suivi infrarouge à 8 canaux IR (https://fr.aliexpress.com/item/1005003333788694.html?scm_id=1007.40000.267768.0&scm-url=1007.40000.267768.0)
Capteur de télémétrie laser ToF | 1 | 2,03 | 2,03 | GY-VL53L0XV2 - I2C (Mauve) | Capteur de télémétrie laser à temps de vol (ToF) 940nm (https://fr.aliexpress.com/item/1005006719586781.html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)
Barettes femelle 20 pins 2,54mm | 3 | 0,17 | 0,52 | Single Row 20 Pin Female Header Socket Pitch 2.54mm | Single Row Pin Female Header Socket Pitch 2.54mm (https://www.aliexpress.com/item/4001198421663.html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)
Connecteur mâle angle droit 6pins | 1 | 0,08 | 0,08 | Right Angle Male Header 6 pin 2,54mm | Right angle Male headers 6Pin (https://www.aliexpress.com/item/1005007569841697.html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)
Batterie 18650 | 1 | 1,85 | 1,85 | Battery Lithium Ion 18650 3,7V 3500mAh | 18650 Lithium Ion Battery for Toys (https://www.aliexpress.com/item/1005007365816245.html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)
Attaches de câble | 2 | 0,01 | 0,02 | Attaches de câble en nylon autobloquant 3x100mm | Attaches de câbles en nylon autobloquant (https://fr.aliexpress.com/item/1005005303239811.html?scm_id=1007.14452.398466.0&scm-url=1007.14452.398466.0)
Vis M3x6mm | 6 | 0,10 | 0,60 | Vis cruciformes à tête ronde en acier inoxydable | Vis cruciformes à tête ronde M3 x 6 (https://fr.aliexpress.com/item/1005003789611708.html)
Vis M3x10mm | 6 | 0,10 | 0,62 | Vis cruciformes à tête ronde en acier inoxydable | Vis cruciformes à tête ronde M3 x 10 (https://fr.aliexpress.com/item/1005003789611708.html)
Rondelles M3 | 6 | 0,02 | 0,12 | Rondelle Plate en Acier Inoxydable DIN125 M3 | Rondelle Plate en Acier Inoxydable (https://fr.aliexpress.com/item/32975752411.html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)
Entretoise nylon noir M3x11mm | 6 | 0,05 | 0,28 | Entretoise en nylon noir M3x11 | 40 Pièces M3 Écrou en Acier Inoxydable (https://fr.aliexpress.com/item/1005003926489930.html)
Prix composants version de base | | | 27,38
Option code d’indentification
LED infrarouge 5mm | 2 | 0,10 | 0,20 | LED IR 5mm 940nm | Diode électroluminescente LED IR (https://fr.aliexpress.com/item/1005003946239993.html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)
Récepteur infrarouge | 1 | 0,20 | 0,20 | TL1838 - Fréquence porteuse : 38 KHz | TL1838 Infrared Receiver (https://fr.aliexpress.com/item/1005006501718320.html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)
Condensateur électrolytique | 1 | 0,10 | 0,10 | 10µf 25V Aluminum Electrolytic Capacitor | 10µf 25V capacitor (https://www.aliexpress.com/item/1005006203199812.html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)
Prix composants option | | | 0,49
PCB assemblé SMD
PCB double face gravé | 1 | 0,61 | 0,61 | Gerber_PCB1_2024-06-16 | Gerber_PCB1_2024-06-16.zip (https://github.com/Versatilerobot/TwinBristleBot/blob/f80b584be0ccc95bc99f441bce5966740ef62b1b/PCB/Gerber_PCB1_2024-06-16.zip)
Tous les composants SMD assemblés | 1 | 2,92 | 2,92 | BOM_TTB3.1_PCB1_2024-06-16 | PickAndPlace_PCB1_2024-06-16_SMD-only.xlsx (https://github.com/Versatilerobot/TwinBristleBot/blob/94f209d313d76e8f80e0b64e5a1752f9c5207bc9/PCB/PickAndPlace_PCB1_2024-06-16_SMD-only.xlsx)
Frais de port & taxes | 1 | 4,10 | 4,10 | | JLCPCB (https://jlcpcb.com/)
Prix PCB et SMD assemblés | | | 7,63
Piéces 3D raw material | Quantité
| par robot | Prix
| | Unitaire € | Prix total
| | | € | Notes
| | | | A titre indicatif seulement - Imprimante Flsun FQQ Pro | Exemples de fourniture
Corps | 1 | 0,63 | 0,63 | 8,47m PLA 2h00 | SUNLU Meta Filament PLA 1,75 mm (https://www.amazon.fr/dp/B0B24Y84LN/ref=twister_B0B87C7YH4?_encoding=UTF8&th=1)
Pattes | 2 | 0,23 | 0,45 | 2,95m TPU Blanc 1h36 | ERYONE TPU Filament 1.75mm (https://www.amazon.fr/ERYONE-Filament-1-75mm-Drucker-0-05mm/dp/B07WDF31WP?hvadid=411298501561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)
Prix matiére | 3 | | 1,08
Energie pour imprimer les piéces electricité | Quantité
| par robot | Prix
| | Unitaire € | Prix total
| | | € | Notes
| | | | A titre indicatif seulement - Imprimante Flsun FQQ Pro
Prix énergie | 3,5 | 0,03 | 0,11
Total | | | 36,69 | A titre indicatif seulement

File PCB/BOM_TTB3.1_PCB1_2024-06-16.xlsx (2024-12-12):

No. | Quantity | Comment | Designator | Footprint | Value | Manufacturer Part | Manufacturer | Supplier Part | Supplier
1 | 1 | 220uF | C1 | CAP-TH_BD6.3-P2.50-D1.0-FD | 220uF | KM227M025E11RR0VH2FP0 | CX(承兴) | C12450 | LCSC
2 | 2 | 100nF | C2,C3 | C0603 | 100nF | CC0603KRX7R9BB104 | YAGEO(国巨) | C14663 | LCSC
3 | 1 | 10uF | C4 | CAP-SMD_L3.2-W1.6-RD-C7171 | 10uF | TAJA106K016RNJ | Kyocera AVX | C7171 | LCSC
4 | 2 | 1N5819W | D1,D2 | SOD-123_L2.7-W1.6-LS3.7-R-RD |  | 1N5819W | ZHIDE(志得) | C2683619 | LCSC
5 | 2 | BX-PM2.54-1-20PY | H1,H2 | HDR-TH_20P-P2.54-V-F |  | BX-PM2.54-1-20PY | Bossie(博锡) | C18078139 | LCSC
6 | 1 | 22052061 | H3 | hdr-th_6p-p2.54-h-m-w9.5 |  | 22052061 | MOLEX | C586989 | LCSC
7 | 1 | BX-PM2.54-1-11PY | H4 | HDR-TH_11P-P2.54-V-F-1 |  | BX-PM2.54-1-11PY | Bossie(博锡) | C18078133 | LCSC
8 | 2 | KH-2.54PH180-1X4P-L11.5 | H5,H6 | hdr-th_4p-p2.54-v-m |  | KH-2.54PH180-1X4P-L11.5 | kinghelm(金航标) | C2905435 | LCSC
9 | 2 | IR204-A | LED1,LED2 | led-th_bd4.8-p2.54-fd |  | IR204-A | EVERLIGHT(亿光) | C264278 | LCSC
10 | 1 | NCD0805R1 | LED3 | LED0805-R-RD |  | NCD0805R1 | 国星光电 | C84256 | LCSC
11 | 1 | KT-0805G | LED4 | LED0805-R-RD |  | KT-0805G | KENTO | C2297 | LCSC
12 | 3 | AO3400A | Q1,Q2,Q3 | SOT-23-3_L2.9-W1.6-P1.90-LS2.8-BR |  | AO3400A | AOS | C20917 | LCSC
13 | 2 | 0Ω | R2,R18 | R0402 | 0Ω | 0402WGF0000TCE | UNI-ROYAL(厚声) | C17168 | LCSC
14 | 4 | 220Ω | R3,R4,R9,R13 | R0603 | 220Ω | 0603WAF2200T5E | UNI-ROYAL(厚声) | C22962 | LCSC
15 | 3 | 47kΩ | R5,R6,R14 | R0603 | 47kΩ | 0603WAF4702T5E | UNI-ROYAL(厚声) | C25819 | LCSC
16 | 2 | 270Ω | R11,R12 | R0603 | 270Ω | 0603WAF2700T5E | UNI-ROYAL(厚声) | C22966 | LCSC
17 | 1 | 33Ω | R17 | R0402 | 33Ω | 0402WGF330JTCE | UNI-ROYAL(厚声) | C25105 | LCSC
18 | 6 | Screw-Hole-M3 | SCREW1,SCREW2,SCREW3,SCREW4,SCREW5,SCREW6 | Screw-Hole-M3
19 | 1 | TSOP38238 | TSOP | SENSOR-TG_TSOP38236 |  | TSOP38238 | VISHAY(威世) | C141632 | LCSC
20 | 2 | BX-XH2.54-2PZZ | U1,U2 | CONN-TH_2P-P2.50_BX-XH2.54-2PZZ |  | BX-XH2.54-2PZZ | Bossie(博锡) | C18077833 | LCSC

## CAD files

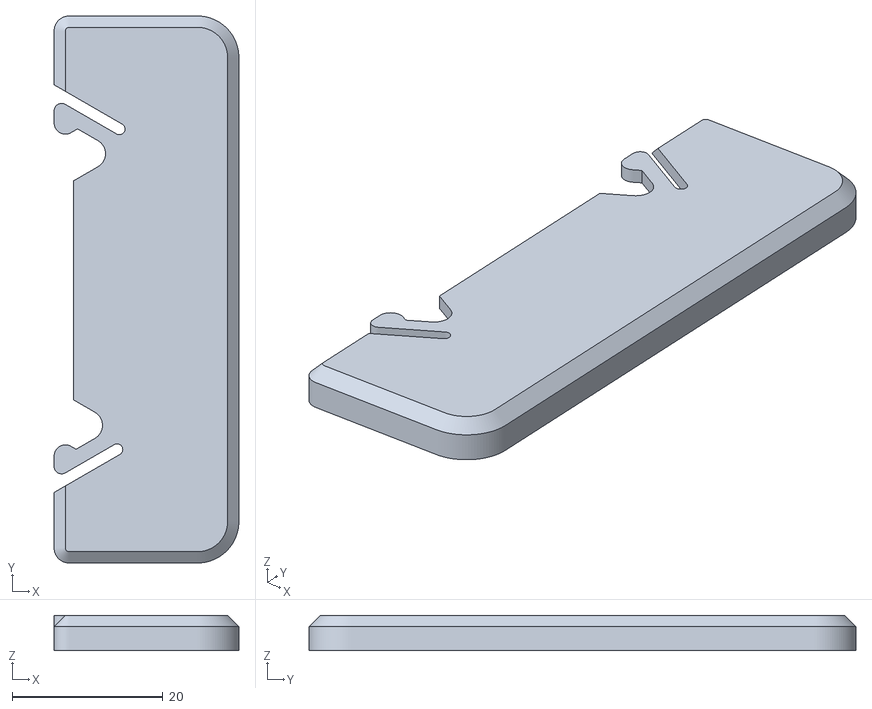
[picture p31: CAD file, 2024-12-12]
3D_STL/Shield.stl
24.5 x 72.5 x 4.70

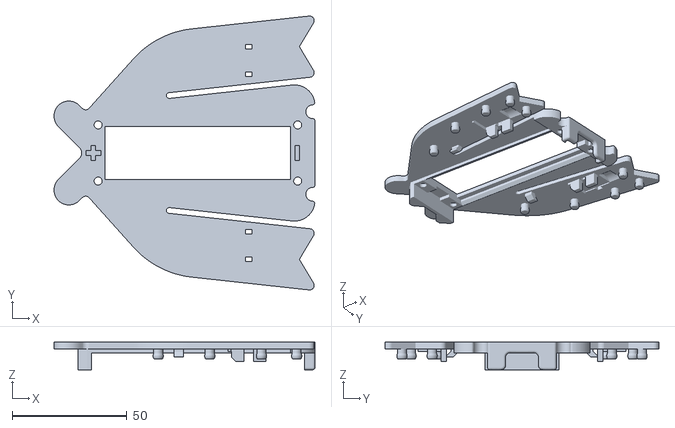
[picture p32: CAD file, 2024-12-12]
3D_STL/Body.stl
113.8 x 119.4 x 12.0

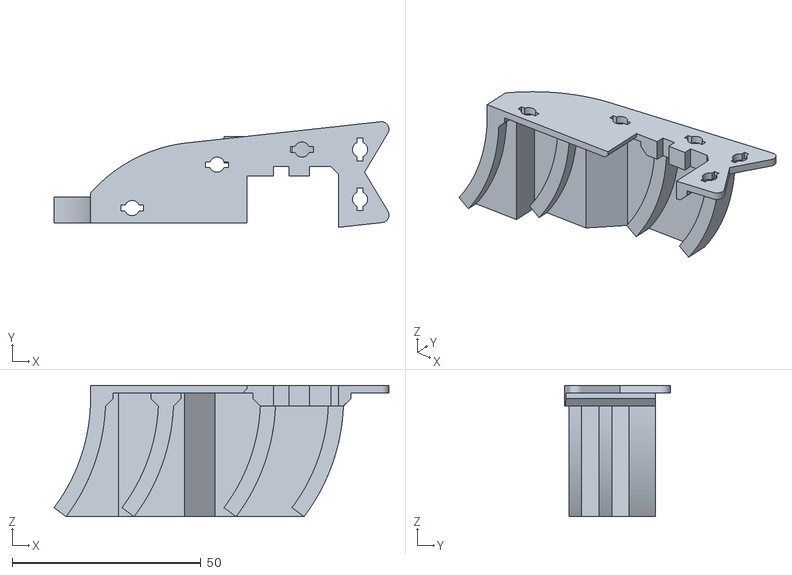
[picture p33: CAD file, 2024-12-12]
3D_STL/Leg_L.stl
88.7 x 28.0 x 34.8

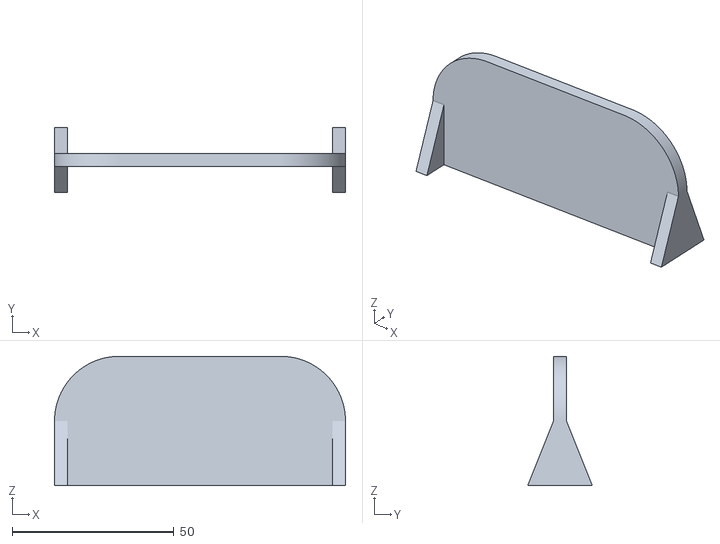
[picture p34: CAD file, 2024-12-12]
3D_STL/Stopper.stl
90.0 x 20.0 x 40.0

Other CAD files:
3D_STL/Leg_R.stl

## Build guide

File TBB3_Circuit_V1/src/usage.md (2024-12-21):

Usage Notes
===========

Calibration
-----------

This library allows you to use the QTRSensors::calibrate() method to easily calibrate your sensors for the particular conditions it will encounter. Calibrating your sensors can lead to substantially more reliable sensor readings, which in turn can help simplify your code. As such, we recommend you build a calibration phase into your application’s initialization routine. This can be as simple as a fixed duration over which you repeatedly call the `calibrate()` method. During this calibration phase, you will need to expose each of your reflectance sensors to the lightest and darkest readings they will encounter. For example, if you have made a line follower, you will want to slide it across the line during the calibration phase so the each sensor can get a reading of how dark the line is and how light the ground is. A sample calibration routine would be:

```cpp
#include <QTRSensorsESP32.h>

QTRSensors qtr;

void setup()
{
  // Optional: wait for some input from the user, such as a button press.

  // Initialize the sensors.
  // In this example we have three sensors on pins A0 - A2.
  qtr.setTypeRC(); // or setTypeAnalog()
  qtr.setSensorPins((const uint8_t[]){A0, A1, A2}, 3);

  // Optional: change parameters like RC timeout, set an emitter control pin...

  // Then start the calibration phase and move the sensors over both reflectance
  // extremes they will encounter in your application. This calibration should
  // take about 5 seconds (250 iterations * 20 ms per iteration).
  //
  // Passing a QTRReadMode to calibrate() is optional; it should match the mode
  // you plan to use when reading the sensors.
  for (uint8_t i = 0; i < 250; i++)
  {
    qtr.calibrate();
    delay(20);
  }

  // Optional: signal that the calibration phase is now over and wait for
  // further input from the user, such as a button press.
}
```

Reading the sensors
-------------------

This library gives you a number of different ways to read the sensors. All of these take an optional `mode` argument that determines how the IR emitters behave during the reading. (The options available depend on what sensor board you have; see ::QTRReadMode for details.)

1. You can request raw sensor values using the QTRSensors::read() method.

2. You can request calibrated sensor values using the QTRSensors::readCalibrated() method. Calibrated sensor values will always range from 0 to 1000, with 0 corresponding to the most reflective (brightest) surface encountered during calibration, and 1000 corresponding to the least reflective (darkest).

3. For line-detection applications, you can request the line location using the QTRSensors::readLineBlack() or QTRSensors::readLineWhite() methods. These are intended for use with a black line on a white background or a white line on a black background, respectively. Each of these methods provides calibrated readings for each sensor and returns an integer that tells you where it thinks the line is. If you are using N sensors, a returned value of 0 means it thinks the line is on or to the outside of sensor 0, and a returned value of 1000 &times; (N&minus;1) means it thinks the line is on or to the outside of sensor N&minus;1. As you slide your sensors across the line, the line position will change monotonically from 0 to 1000 &times; (N&minus;1), or vice versa. This line-position value can be used for closed-loop PID control.

A sample routine to obtain the sensor values and perform rudimentary line following would be:

```cpp
void loop()
{
  uint16_t sensors[3];
  // Get calibrated sensor values returned in the sensors array, along with the
  // line position, which will range from 0 to 2000, with 1000 corresponding to
  // a position under the middle sensor.
  int16_t position = qtr.readLineBlack(sensors);

  // If all three sensors see very low reflectance, take some appropriate action
  // for this  situation.
  if ((sensors[0] > 750) && (sensors[1] > 750) && (sensors[2] > 750))
  {
    // Do something. Maybe this means we're at the edge of a course or about to
    // fall off a table, in which case we might want to stop moving, back up,
    // and turn around.
    return;
  }

  // Compute our "error" from the line position. We will make it so that the
  // error is zero when the middle sensor is over the line, because this is our
  // goal. Error will range from -1000 to +1000. If we have sensor 0 on the left
  // and sensor 2 on the right,  a reading of -1000 means that we see the line
  // on the left and a reading of +1000 means we see the line on the right.
  int16_t error = position - 1000;

  int16_t leftMotorSpeed = 100;
  int16_t rightMotorSpeed = 100;
  if (error < -500)
  {
    // the line is on the left
    leftMotorSpeed = 0;  // turn left
  }
  if (error > 500)
  {
    // the line is on the right
    rightMotorSpeed = 0;  // turn right
  }

  // set motor speeds using the two motor speed variables above
}
```

PID Control
-----------

The integer value returned by QTRSensors::readLineWhite() or QTRSensors::readLineBlack() can be easily converted into a measure of your position error for line-following applications, as was demonstrated in the previous code sample. The function used to generate this position/error value is designed to be monotonic, which means the value will almost always change in the same direction as you sweep your sensors across the line. This makes it a great quantity to use for PID (proportional&ndash;integral&ndash;derivative) control.

Explaining PID control is beyond the scope of this document, but Wikipedia has a good [article](https://en.wikipedia.org/wiki/PID_controller) on the subject.

The following code gives a very simple example of PD (proportional&ndash;derivative) control (we find the integral term is usually not necessary for line following). The specific constants will be determined by your particular application, but note that the derivative constant Kd is usually much bigger than the proportional constant Kp. This is because the derivative (rate of change) of the error is a much smaller quantity than the error itself, so in order to produce a meaningful correction, it needs to be multiplied by a much larger constant.

```cpp

void loop()
{
  static uint16_t lastError = 0;

  uint16_t sensors[3];
  // Get calibrated sensor values returned in the sensors array, along with the
  // line position, which will range from 0 to 2000, with 1000 corresponding to
  // a position under the middle sensor
  int16_t position = qtr.readLineBlack(sensors);

  // Compute our "error" from the line position. We will make it so that the
  // error is zero when the middle sensor is over the line, because this is our
  // goal. Error will range from -1000 to +1000. If we have sensor 0 on the left
  // and sensor 2 on the right, a reading of -1000 means that we see the line on
  // the left and a reading of +1000 means we see the line on the right.
  int16_t error = position - 1000;

  // Set the motor speed based on proportional and derivative PID terms:
  // KP is the floating-point proportional constant (maybe start with a value around 0.1)
  // KD is the floating-point derivative constant (maybe start with a value around 5)
  // Note that when doing PID, it is very important you get your signs right, or
  // else the control loop will be unstable.
  int16_t motorSpeed = KP * error + KD * (error - lastError);
  lastError = error;

  // M1 and M2 are base motor speeds (the speeds the motors should run if you
  // are perfectly on the line with no error). If your motors are well matched,
  // M1 and M2 will be equal. When you start testing your PID loop, it might
  // help to start with small values for M1 and M2. You can then increase the
  // speed as you fine-tune your PID constants KP and KD.
  int16_t m1Speed = M1 + motorSpeed;
  int16_t m2Speed = M2 - motorSpeed;

  // It might help to keep the speeds positive (this is optional). You might
  // also want to add a similar check to keep the speeds from exceeding a
  // maximum limit.
  if (m1Speed < 0) { m1Speed = 0; }
  if (m2Speed < 0) { m2Speed = 0; }

  // set motor speeds using the two motor speed variables above
}
```

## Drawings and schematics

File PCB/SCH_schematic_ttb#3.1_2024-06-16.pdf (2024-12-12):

# TwinBristleBot#3.1

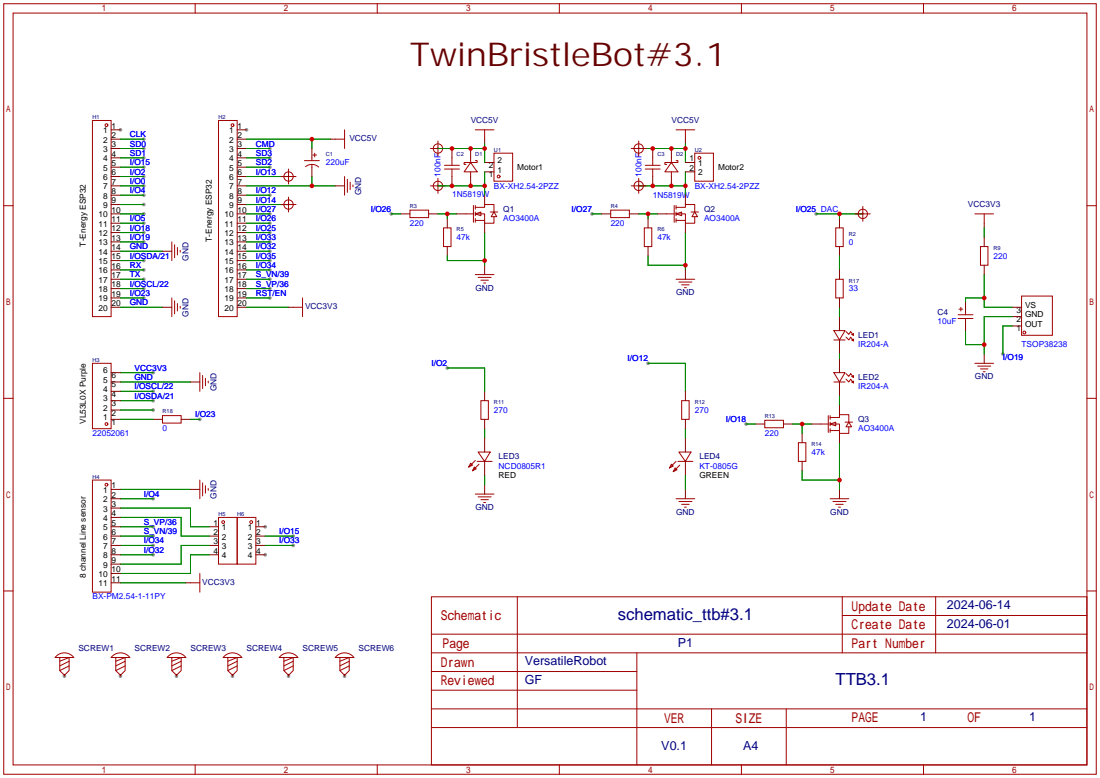
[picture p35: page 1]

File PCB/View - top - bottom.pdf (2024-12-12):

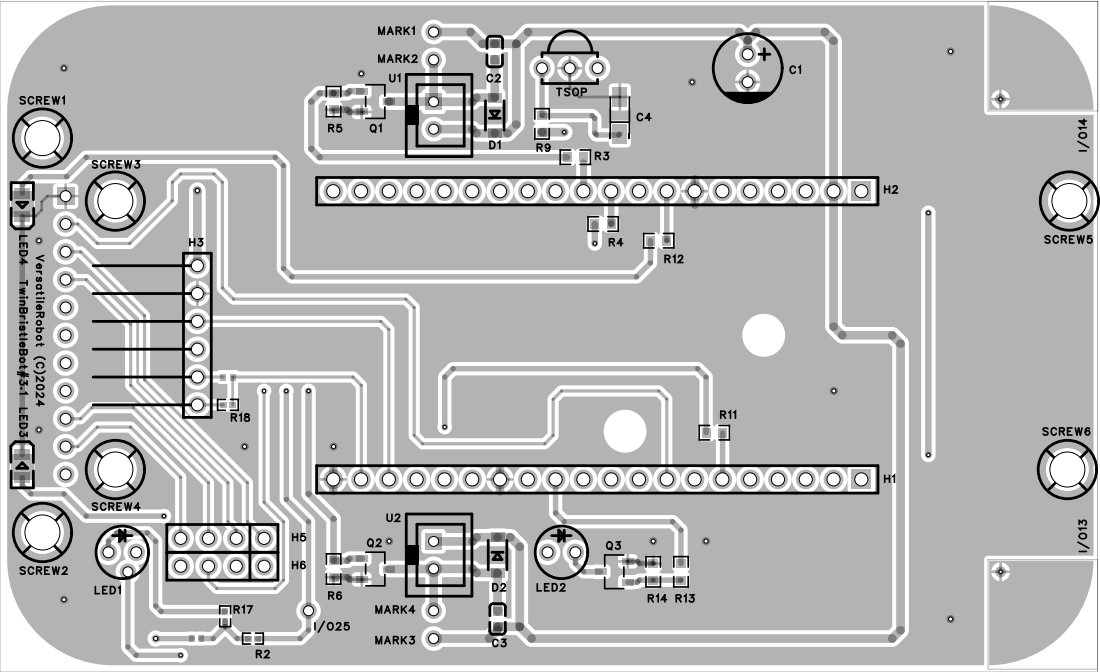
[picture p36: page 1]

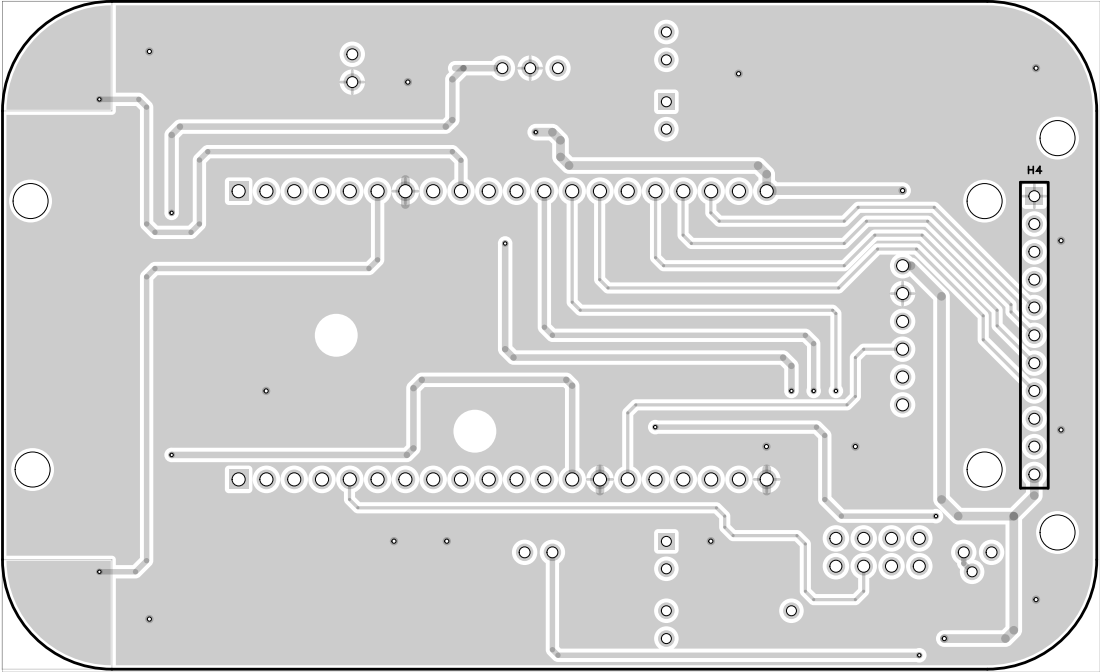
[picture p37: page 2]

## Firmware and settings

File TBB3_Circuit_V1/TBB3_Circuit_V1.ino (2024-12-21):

/* Sketch TBB#3
   VersatileRobot Dec.7th, 2024

   MIT License
   Copyright (c) 2024 Versatilerobot
  
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
   THE SOFTWARE IS PROVIDED "AS IS", WITHOUT WARRANTY OF ANY KIND, EXPRESS OR
   IMPLIED, INCLUDING BUT NOT LIMITED TO THE WARRANTIES OF MERCHANTABILITY,
   FITNESS FOR A PARTICULAR PURPOSE AND NONINFRINGEMENT. IN NO EVENT SHALL THE
   AUTHORS OR COPYRIGHT HOLDERS BE LIABLE FOR ANY CLAIM, DAMAGES OR OTHER
   LIABILITY, WHETHER IN AN ACTION OF CONTRACT, TORT OR OTHERWISE, ARISING FROM,
   OUT OF OR IN CONNECTION WITH THE SOFTWARE OR THE USE OR OTHER DEALINGS IN THE
   SOFTWARE.   
*/

#include <Wire.h>
#include <VL53L0X.h>
#include "src/QTRSensorsESP32.h"      // Pololu libray that i modified to be compatible with 12 bits ESP32 (4096 resolution)

// Battery check
#define PIN_ADC_BAT 35                // Pin connected to battery inside the T-Energy module
#define BlueLed 5                     // Inboard LED used as indicator of discharge
int in = 0;                           // Value read on battery pin 
int batteryLevelSamples = 5;          // Sampling level of battery reads
float v_bat = 0;                      // Converted battery voltage (V)
bool warnBat = LOW;                   // Battery discharged warning
volatile unsigned long timerBat = 0;  // Time from last battery check

// Analog QTR line sensors instance
QTRSensors qtr;
const uint8_t SensorCount = 4;
uint16_t sensorValues[SensorCount];
uint16_t KP = 0.2;                    // Proportional - start by 0.1
uint16_t KD = 3;                      // Derivate - start by 3
int16_t lastError = 0;                // Previous error level of position on the line


// Front LED pins
int RedLedPin = 2;
int GreenLedPin = 12;
volatile unsigned long timerBlinkSpeed = 0;

// Capacitive button sensors
int startButton = 14;                 // Inverted for avoid conflict when switching
int modeButton = 13;                  // Used for set speed
int threshold = 45;                   // Level of touch detection
bool startdetected = LOW;
bool previoustart = LOW;
bool speedSelect = LOW;
volatile unsigned long sinceLastTouchStart = 0;
volatile unsigned long sinceLastTouchSelector = 0;

// Motor pins
int motorPinLeft = 27;
int motorPinRight = 26; 

// Motor PWM properties for ESP32
const int freq = 20000;
const int MotorL = 0;                 // channel 0
const int MotorR = 1;                 // channel 1
const int resolution = 8;
int PWM []= {95, 110, 120};           // Speed values - Low, Medium, High
int dutyCycle = PWM [1];              // Default Medium
int pointer = 1;

// Motor speed
int16_t leftMotorSpeed = 0;
int16_t rightMotorSpeed = 0;

// Tof VL53L0X instance with XSHUT standby
VL53L0X sensor;
#define XSHUT 23
bool XSHUT_STATE = HIGH;
uint16_t Sensor_Offset = 42;          // Distance offset (mm)
uint16_t measureDistance = 0;         // Value to store the measured distance
uint16_t obstacle = 110;              // Warning distance treshold (mm)
bool warnObstacle = LOW;              // Obstacle warning
bool object = LOW;                    // Obstacle detection
unsigned long timerTof = 0;           // Time from last distance check
unsigned long periodObjCheck = 50;    // Period at witch check the object detection

// ------------------------------------------

void setup() {

  Serial.begin(115200);  
  Wire.begin();
  
  // Set VL53L0X 
  pinMode(XSHUT, OUTPUT);             // Standby pin 
  digitalWrite(XSHUT, XSHUT_STATE);
  delay(50);
  sensor.init();
  // Set timeout  
  if (!sensor.init())
  {
    Serial.println(F("Failed to detect and initialize sensor!"));
    while (1) {}
  }
  sensor.setTimeout(100);
  // Set Tof higher speed at the cost of lower accuracy
  // reduce timing budget to 10 ms (default is about 33 ms)
  sensor.setMeasurementTimingBudget(10000);
  // Set the minimum amplitude of the signal reflected from the target and received by the sensor necessary for it to report a valid reading 
  // Units of MCPS (mega counts per second). Useful for reduce measurement error (default is 0.25 MCPS)
  sensor.setSignalRateLimit(2.5);  
  
  // Set battery pins and check
  pinMode(PIN_ADC_BAT, INPUT);
  pinMode(BlueLed,OUTPUT);
  read_adc_bat();
  if (warnBat == HIGH){
    while (1==1);
  }
  
  // Set capacitive touch interrupt for start bouton
  touchAttachInterrupt(startButton, gotTouch, threshold);

  // Configure the line sensors
  qtr.setTypeAnalog();
  qtr.setSensorPins((const uint8_t[]){36, 39, 34, 32}, SensorCount);
  qtr.setEmitterPin(4);

  delay(500);
  
  // Set the motor pin as output
  pinMode(motorPinLeft, OUTPUT);
  pinMode(motorPinRight, OUTPUT);  
  
  // Configure motor PWM functionalities - specific ESP32
  ledcSetup(MotorL, freq, resolution);
  ledcSetup(MotorR, freq, resolution);  
  
  // Attach the channel to the GPIO to be controlled
  ledcAttachPin(motorPinLeft, MotorL);
  ledcAttachPin(motorPinRight, MotorR);

  // Set front LED pins
  pinMode(RedLedPin, OUTPUT);
  pinMode(GreenLedPin, OUTPUT);

  // Calibrate the QTR line sensors
  digitalWrite(RedLedPin, HIGH);       // Turn on Front LED to indicate we are in calibration mode
  digitalWrite(GreenLedPin, HIGH);     // Turn on Front LED to indicate we are in calibration mode
  for (uint16_t i = 0; i < 200; i++)   // Calibration loop
  {
    qtr.calibrate();
  }
  digitalWrite(RedLedPin, LOW);        // Turn off Front LED to indicate we are through with calibration
  digitalWrite(GreenLedPin, LOW);      // Turn off front LED to indicate we are through with calibration

  // Indicate sketch uploaded
  Serial.println("TBB3_Circuit_V1.ino");
  Serial.println(F(__FILE__ " " __DATE__ " " __TIME__));
    
  // Indicate min and max values per sensor - can be skip
  for (uint8_t i = 0; i < SensorCount; i++)
  {
    Serial.print(qtr.calibrationOn.minimum[i]); // maximum reflectance (i.e. whiter)
    Serial.print(' ');
  }
  Serial.println();
  for (uint8_t i = 0; i < SensorCount; i++)
  {
    Serial.print(qtr.calibrationOn.maximum[i]); // minimum reflectance (i.e. blacker)
    Serial.print(' ');
  }
  Serial.println();
  Serial.println();
  delay(1000);
timerBat = millis();                  // init timer
  timerTof = timerBat;                // init timer
}

// ---------------------------------------------

void loop() {

  qtr.emittersOff(); // Turn Off line sensor for reduce the current load
  frontLed();
  read_adc_bat();
  read_obstacle();
   
  if (startdetected && !warnBat && !object){  // ON      
    if (!previoustart) previoustart = HIGH;   
    qtr.emittersOn();                         // Turn On line sensor
    // Get calibrated sensor values returned in the sensors array, along with the line position
    // Position will range from 0 to 3000, with 1500 corresponding to the line over the two middle sensors of module
    uint16_t position = qtr.readLineBlack(sensorValues); 
    // Compute our "error" from the line position. We will make it so that the error is zero when
    // the two middle sensors are over the line, because this is our goal.  Error will range from -1500 to +1500.
    int16_t error = position - 1500;          // error level of position on the line 

    // avoid drift
    if (error >= 1450 || error <=-1450) {
      dutyCycle = PWM [0];                    // Set low speed        
      }
      else {
        dutyCycle = PWM [pointer];            // Set the base motor speed
        }
     
     // Slow down if suspition of obstacle
     if (warnObstacle == HIGH){
      dutyCycle = PWM [0];                    // Set low speed
     }
        
    // Normalized error    
    error = error * dutyCycle / 1500;

    // Set the motor speed based on proportional and derivative PID terms:
    // KP is the floating-point proportional constant
    // KD is the floating-point derivative constant
    // KP + KD = 1
    // Note that when doing PID, it is very important you get your signs right, or
    // else the control loop will be unstable.
    int16_t motorSpeed = 0.6 * error + 0.4 * (error - lastError);
    lastError = error;

    // DutyCycle is base motor speed (the speed the motors should run if you
    // are perfectly on the line with no error).
    // When you start testing your PID loop, it might help to start with small
    // values for dutyCycle. You can then increase the speed as you fine-tune 
    // your PID constants KP and KD.
    leftMotorSpeed = dutyCycle - motorSpeed;
    rightMotorSpeed = dutyCycle + motorSpeed;
    
    // Keep the speed positive and add a similar check to keep the speeds 
    // from exceeding a maximum limit.
    if (leftMotorSpeed < 0) { leftMotorSpeed = 0; }
    if (rightMotorSpeed < 0) { rightMotorSpeed = 0; }
    if (leftMotorSpeed > 255) { leftMotorSpeed = 255; }
    if (rightMotorSpeed > 255) { rightMotorSpeed = 255; }    
           
    // Set motor speeds using the two motor speed variables above      
    ledcWrite(MotorL, leftMotorSpeed); 
    ledcWrite(MotorR, rightMotorSpeed); 
  }
  else { 
    if (previoustart){
      ledcWrite(MotorL, 0);                   // stop
      ledcWrite(MotorR, 0);                   // stop
      previoustart = LOW;
    } 
    speedSelector();                          // Speed selection when stopped
  }
}

//------------------------------------------------------------------

void gotTouch() {
  if (millis() - sinceLastTouchStart < 500) return; // simple debounce
  startdetected = !startdetected;
  sinceLastTouchStart = millis();  
}

void speedSelector() {
  if (millis() - sinceLastTouchSelector < 500) return; // simple debounce
  if(touchRead(modeButton) < threshold && speedSelect == LOW){
//      Serial.println("touch"); 
      speedSelect = HIGH;
      pointer++;
      if (pointer>2) pointer=0;
      dutyCycle = PWM [pointer];
      }
      else if (speedSelect == HIGH){
      speedSelect = LOW;
      }
//  Serial.println(PWM [pointer]);    
  sinceLastTouchSelector = millis();  
}

void frontLed() {
  if (previoustart == HIGH){      
    if (abs(leftMotorSpeed-rightMotorSpeed) < 50){
      // go straight
      digitalWrite(RedLedPin, HIGH);
      digitalWrite(GreenLedPin, HIGH);
    }
    else if (leftMotorSpeed > rightMotorSpeed){
      // turn right
      digitalWrite(RedLedPin, LOW);
      digitalWrite(GreenLedPin, HIGH);
    }
    else if (leftMotorSpeed < rightMotorSpeed){
      // turn left
      digitalWrite(RedLedPin, HIGH);
      digitalWrite(GreenLedPin, LOW);    
    }
  }
  else{  
      // Blinking speed selected
    digitalWrite(RedLedPin, LOW);
    digitalWrite(GreenLedPin, LOW); 
    int LED = RedLedPin;
    for (int loop=0; loop<2; loop++){
      for (int i=0; i<pointer+1; i++){
      timerBlinkSpeed = millis();
      while(millis() - timerBlinkSpeed < 400){
      if (startdetected == HIGH)return;
      }
      digitalWrite(LED,!digitalRead(LED));
      timerBlinkSpeed = millis();
      while(millis() - timerBlinkSpeed < 400){
      if (startdetected == HIGH)return;
      }
      digitalWrite(LED,!digitalRead(LED));
      }
      LED = GreenLedPin;
    }
  }
}

void read_obstacle(){
  if (millis() - timerTof < periodObjCheck) return;    
  if (periodObjCheck == 2000) periodObjCheck = 50; 
  // One shoot measurement for save time 
  measureDistance = sensor.readRangeSingleMillimeters()- Sensor_Offset;   
// Serial.println(measureDistance);
    if (measureDistance < obstacle && !sensor.timeoutOccurred()) { 
      if (warnObstacle == HIGH){
      periodObjCheck = 2000;                  // waiting time for restart
      object = HIGH;                          // obstacle detected
      }
    warnObstacle = HIGH;                      // suspition of obstacle
    }
    else {
      warnObstacle = LOW;
      object = LOW;
      }  
  timerTof = millis();
}

void read_adc_bat() {
if (millis() - timerBat < 30000) return;
for (int i = 0; i < batteryLevelSamples; i++){
in += analogRead(PIN_ADC_BAT);
}
v_bat = (float)in /(4096*batteryLevelSamples) * 2 * 3.7; // resolution; sampling; internal divider; nominal voltage 18650
in = 0;
if (v_bat < 3 && warnBat == LOW ){
  warnBat = HIGH;  
  digitalWrite(BlueLed, HIGH);               // Warn battery discharged
}
else if(v_bat < 3 && warnBat == HIGH ){ 
  digitalWrite(BlueLed, LOW);                
  digitalWrite(RedLedPin, LOW);
  digitalWrite(GreenLedPin, LOW);   
  while (1==1);                              // Please switch off the robot and go to battery charge
}
else {
  digitalWrite(BlueLed, LOW);  
  }
timerBat = millis();
}

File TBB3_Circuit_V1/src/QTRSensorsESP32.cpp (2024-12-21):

#include "QTRSensorsESP32.h"
#include <Arduino.h>

void QTRSensors::setTypeRC()
{
  _type = QTRType::RC;
  _maxValue = _timeout;
}

void QTRSensors::setTypeAnalog()
{
  _type = QTRType::Analog;
  _maxValue = 4095; // ESP32 analogRead() returns a 12-bit value by default
}

void QTRSensors::setSensorPins(const uint8_t * pins, uint8_t sensorCount)
{
  if (sensorCount > QTRMaxSensors) { sensorCount = QTRMaxSensors; }

  // (Re)allocate and initialize the array if necessary.
  uint8_t * oldSensorPins = _sensorPins;
  _sensorPins = (uint8_t *)realloc(_sensorPins, sizeof(uint8_t) * sensorCount);
  if (_sensorPins == nullptr)
  {
    // Memory allocation failed; don't continue.
    free(oldSensorPins); // deallocate any memory used by old array
    return;
  }

  for (uint8_t i = 0; i < sensorCount; i++)
  {
    _sensorPins[i] = pins[i];
  }

  _sensorCount = sensorCount;

  // Any previous calibration values are no longer valid, and the calibration
  // arrays might need to be reallocated if the sensor count was changed.
  calibrationOn.initialized = false;
  calibrationOff.initialized = false;
}

void QTRSensors::setTimeout(uint16_t timeout)
{
  if (timeout > 32767) { timeout = 32767; }
  _timeout = timeout;
  if (_type == QTRType::RC) { _maxValue = timeout; }
}

void QTRSensors::setSamplesPerSensor(uint8_t samples)
{
  if (samples > 64) { samples = 64; }
  _samplesPerSensor = samples;
}

void QTRSensors::setEmitterPin(uint8_t emitterPin)
{
  releaseEmitterPins();

  _oddEmitterPin = emitterPin;
  pinMode(_oddEmitterPin, OUTPUT);

  _emitterPinCount = 1;
}

void QTRSensors::setEmitterPins(uint8_t oddEmitterPin, uint8_t evenEmitterPin)
{
  releaseEmitterPins();

  _oddEmitterPin = oddEmitterPin;
  _evenEmitterPin = evenEmitterPin;
  pinMode(_oddEmitterPin, OUTPUT);
  pinMode(_evenEmitterPin, OUTPUT);

  _emitterPinCount = 2;
}

void QTRSensors::releaseEmitterPins()
{
  if (_oddEmitterPin != QTRNoEmitterPin)
  {
    pinMode(_oddEmitterPin, INPUT);
    _oddEmitterPin = QTRNoEmitterPin;
  }

  if (_evenEmitterPin != QTRNoEmitterPin)
  {
    pinMode(_evenEmitterPin, INPUT);
    _evenEmitterPin = QTRNoEmitterPin;
  }

  _emitterPinCount = 0;
}

void QTRSensors::setDimmingLevel(uint8_t dimmingLevel)
{
  if (dimmingLevel > 31) { dimmingLevel = 31; }
  _dimmingLevel = dimmingLevel;
}

// emitters defaults to QTREmitters::All; wait defaults to true
void QTRSensors::emittersOff(QTREmitters emitters, bool wait)
{
  bool pinChanged = false;

  // Use odd emitter pin in these cases:
  // - 1 emitter pin, emitters = all
  // - 2 emitter pins, emitters = all
  // - 2 emitter pins, emitters = odd
  if (emitters == QTREmitters::All ||
      (_emitterPinCount == 2 && emitters == QTREmitters::Odd))
  {
    // Check if pin is defined and only turn off if not already off
    if ((_oddEmitterPin != QTRNoEmitterPin) &&
        (digitalRead(_oddEmitterPin) == HIGH))
    {
      digitalWrite(_oddEmitterPin, LOW);
      pinChanged = true;
    }
  }

  // Use even emitter pin in these cases:
  // - 2 emitter pins, emitters = all
  // - 2 emitter pins, emitters = even
  if (_emitterPinCount == 2 &&
      (emitters == QTREmitters::All || emitters == QTREmitters::Even))
  {
    // Check if pin is defined and only turn off if not already off
    if ((_evenEmitterPin != QTRNoEmitterPin) &&
        (digitalRead(_evenEmitterPin) == HIGH))
    {
      digitalWrite(_evenEmitterPin, LOW);
      pinChanged = true;
    }
  }

  if (wait && pinChanged)
  {
    if (_dimmable)
    {
      // driver min is 1 ms
      delayMicroseconds(1200);
    }
    else
    {
      delayMicroseconds(200);
    }
  }
}

void QTRSensors::emittersOn(QTREmitters emitters, bool wait)
{
  bool pinChanged = false;
  uint16_t emittersOnStart;

  // Use odd emitter pin in these cases:
  // - 1 emitter pin, emitters = all
  // - 2 emitter pins, emitters = all
  // - 2 emitter pins, emitters = odd
  if (emitters == QTREmitters::All ||
      (_emitterPinCount == 2 && emitters == QTREmitters::Odd))
  {
    // Check if pin is defined, and only turn on non-dimmable sensors if not
    // already on, but always turn dimmable sensors off and back on because
    // we might be changing the dimming level (emittersOnWithPin() should take
    // care of this)
    if ((_oddEmitterPin != QTRNoEmitterPin) &&
        ( _dimmable || (digitalRead(_oddEmitterPin) == LOW)))
    {
      emittersOnStart = emittersOnWithPin(_oddEmitterPin);
      pinChanged = true;
    }
  }

  // Use even emitter pin in these cases:
  // - 2 emitter pins, emitters = all
  // - 2 emitter pins, emitters = even
  if (_emitterPinCount == 2 &&
      (emitters == QTREmitters::All || emitters == QTREmitters::Even))
  {
    // Check if pin is defined, and only turn on non-dimmable sensors if not
    // already on, but always turn dimmable sensors off and back on because
    // we might be changing the dimming level (emittersOnWithPin() should take
    // care of this)
    if ((_evenEmitterPin != QTRNoEmitterPin) &&
        (_dimmable || (digitalRead(_evenEmitterPin) == LOW)))
    {
      emittersOnStart = emittersOnWithPin(_evenEmitterPin);
      pinChanged = true;
    }
  }

  if (wait && pinChanged)
  {
    if (_dimmable)
    {
      // Make sure it's been at least 300 us since the emitter pin was first set
      // high before returning. (Driver min is 250 us.) Some time might have
      // already passed while we set the dimming level.
      while ((uint16_t)(micros() - emittersOnStart) < 300)
      {
        delayMicroseconds(10);
      }
    }
    else
    {
      delayMicroseconds(200);
    }
  }
}

// assumes pin is valid (not QTRNoEmitterPin)
// returns time when pin was first set high (used by emittersSelect())
uint16_t QTRSensors::emittersOnWithPin(uint8_t pin)
{
  if (_dimmable && (digitalRead(pin) == HIGH))
  {
    // We are turning on dimmable emitters that are already on. To avoid messing
    // up the dimming level, we have to turn the emitters off and back on. This
    // means the turn-off delay will happen even if wait = false was passed to
    // emittersOn(). (Driver min is 1 ms.)
    digitalWrite(pin, LOW);
    delayMicroseconds(1200);
  }

  digitalWrite(pin, HIGH);
  uint16_t emittersOnStart = micros();

  if (_dimmable && (_dimmingLevel > 0))
  {
    noInterrupts();

    for (uint8_t i = 0; i < _dimmingLevel; i++)
    {
      delayMicroseconds(1);
      digitalWrite(pin, LOW);
      delayMicroseconds(1);
      digitalWrite(pin, HIGH);
    }

    interrupts();
  }

  return emittersOnStart;
}
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

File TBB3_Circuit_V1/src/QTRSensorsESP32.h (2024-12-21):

/// \file QTRSensorsESP32.h

#pragma once

#include <stdint.h>

/// \brief Emitter behavior when taking readings.
///
/// Note that emitter control will only work if you specify a valid emitter pin
/// with setEmitterPin(), and the odd/even modes will only work if you are
/// using a second-generation QTR or QTRX sensor with two emitter control pins
/// and you specify both pins with setEmitterPins().
enum class QTRReadMode : uint8_t {
  /// Each reading is made without turning on the infrared (IR) emitters. The
  /// reading represents ambient light levels near the sensor.
  Off,

  /// Each reading is made with the emitters on. The reading is a measure of
  /// reflectance.
  On,

  /// For each sensor, a reading is made in both the on and off states. The
  /// value returned is **on + max &minus; off**, where **on** and **off** are
  /// the reading with the emitters on and off, respectively, and **max** is
  /// the maximum possible sensor reading. This mode can reduce the amount of
  /// interference from uneven ambient lighting.
  OnAndOff,

  /// The odd-numbered sensors are read with the odd-numbered emitters on, then
  /// the even-numbered sensors are read with the even-numbered emitters on.
  /// This mode can reduce interference between adjacent sensors, especially on
  /// QTRX sensor boards. It is only usable with second-generation QTR and QTRX
  /// sensor arrays that have two emitter control pins.
  OddEven,

  /// The odd and even sensors are read separately with the respective emitters
  /// on, then all sensors are read with emitters off and **on + max &minus;
  /// off** is returned. (In other words, this mode combines OddEven and
  /// OnAndOff.)
  OddEvenAndOff,

  /// Calling read() with this mode prevents it from automatically controlling
  /// the emitters: they are left in their existing states, which allows manual
  /// control of the emitters for testing and advanced use. Calibrating and
  /// obtaining calibrated readings are not supported with this mode.
  Manual
};

/// Sensor types.
enum class QTRType : uint8_t {
  Undefined,
  RC,
  Analog
};

/// Emitters selected to turn on or off.
enum class QTREmitters : uint8_t {
  All,
  Odd,
  Even,
  None
};

/// Represents an undefined emitter control pin.
const uint8_t QTRNoEmitterPin = 255;

/// Default timeout for RC sensors (in microseconds).
const uint16_t QTRRCDefaultTimeout = 2500;

/// The maximum number of sensors supported by an instance of this class.
const uint8_t QTRMaxSensors = 31;

/// \brief Represents a QTR sensor array.
///
/// An instance of this class represents a QTR sensor array, consisting of one
/// or more sensors of the same type. This could be either a single QTR sensor
/// board or multiple boards controlled as a group.
///
/// See \ref md_usage for an overview of how this library can be used and some
/// example code.
class QTRSensors
{
  public:

    QTRSensors() = default;

    ~QTRSensors();

    /// \brief Specifies that the sensors are RC.
    ///
    /// Call this function to set up RC-type sensors.
    void setTypeRC();

    /// \brief Specifies that the sensor type is analog.
    ///
    /// Call this function to set up A-type sensors.
    void setTypeAnalog();

    /// \brief Returns the type of the sensors.
    ///
    /// \return The sensor type as a member of the ::QTRType enum.
    ///
    /// See also setTypeRC() and setTypeAnalog().
    QTRType getType() { return _type; }

    /// \brief Sets the sensor pins.
    ///
    /// \param[in] pins A pointer to an array containing the Arduino pins that
    /// the sensors are connected to.
    ///
    /// \param sensorCount The number of sensors, which should match the length
    /// of the pins array.
    ///
    /// Example usage:
    /// ~~~{.cpp}
    /// // Set pins for four RC sensors connected to pins 6, 7, A0, and A1.
    /// // (Most analog pins can also be used as digital pins.)
    /// qtr.setTypeRC();
    /// qtr.setSensorPins((const uint8_t[]){6, 7, A0, A1}, 4);
    /// ~~~
    /// ~~~{.cpp}
    /// // Set pins for four analog sensors connected to pins A2, A3, A4, and A5.
    /// qtr.setTypeAnalog();
    /// qtr.setSensorPins((const uint8_t[]){A2, A3, A4, A5}, 4);
    /// ~~~
    ///
    /// If \link CalibrationData calibration data \endlink has already been
    /// stored, calling this method will force the storage for the calibration
    /// values to be reallocated and reinitialized the next time calibrate() is
    /// called (it sets `calibrationOn.initialized` and
    /// `calibrationOff.initialized` to false).
    void setSensorPins(const uint8_t * pins, uint8_t sensorCount);

    /// \brief Sets the timeout for RC sensors.
    ///
    /// \param timeout The length of time, in microseconds, beyond which you
    /// consider the sensor reading completely black.
    ///
    /// If the pulse length for a pin exceeds \p timeout, pulse timing will
    /// stop and the reading for that pin will be considered full black. It is
    /// recommended that you set \p timeout to be between 1000 and 3000
    /// &micro;s, depending on factors like the height of your sensors and
    /// ambient lighting. This allows you to shorten the duration of a
    /// sensor-reading cycle while maintaining useful measurements of
    /// reflectance. The default timeout is 2500 &micro;s.
    ///
    /// The maximum allowed timeout is 32767.
    /// (This prevents any possibility of an overflow when using
    /// QTRReadMode::OnAndOff or QTRReadMode::OddEvenAndOff).
    ///
    /// The timeout setting only applies to RC sensors.
    void setTimeout(uint16_t timeout);

    /// \brief Returns the timeout for RC sensors.
    ///
    /// \return The RC sensor timeout in microseconds.
    ///
    /// See also setTimeout().
    uint16_t getTimeout() { return _timeout; }

    /// \brief Sets the number of analog readings to average per analog sensor.
    ///
    /// \param samples The number of 10-bit analog samples (analog-to-digital
    /// conversions) to average per sensor each time it is read.
    ///
    /// Increasing \p samples increases noise suppression at the cost of sample
    /// rate. The maximum number of samples per sensor is 64; the default is 4.
    ///
    /// The samples per sensor setting only applies to analog sensors.
    void setSamplesPerSensor(uint8_t samples);

    /// \brief Returns the number of analog readings to average per analog
    /// sensor.
    ///
    /// \return The samples per channel for analog sensors.
    ///
    /// See also setSamplesPerSensor().
    uint16_t getSamplesPerSensor() { return _samplesPerSensor; }
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

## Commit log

2024-12-12 Rename Pattes D.stl to Patte_D.stl
    [Patte_D.stl]
2024-12-12 Rename Pattes G.stl to Patte_G.stl
    [Patte_G.stl]
